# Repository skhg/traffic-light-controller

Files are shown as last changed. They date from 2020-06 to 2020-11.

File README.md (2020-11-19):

# traffic-light-controller

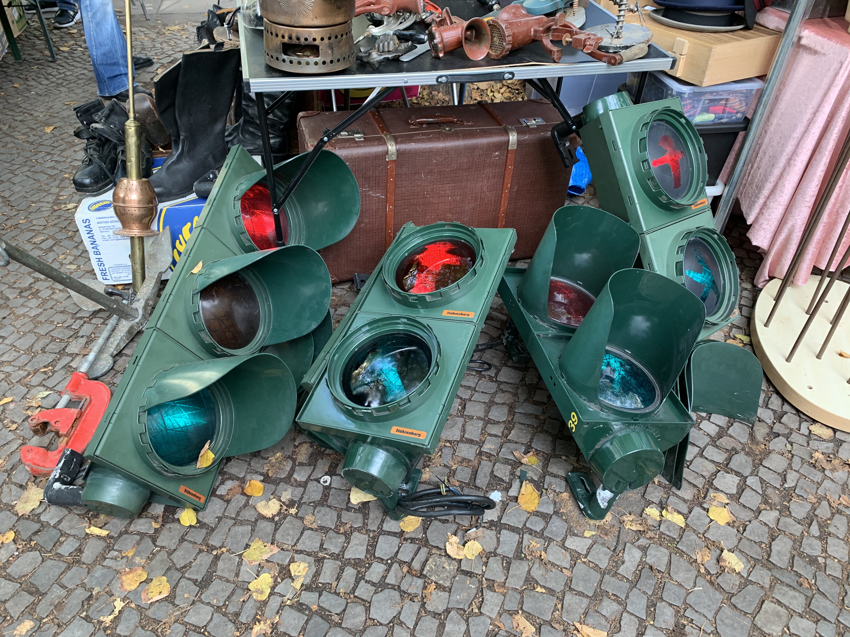
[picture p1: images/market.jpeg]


The [_Ampelmännchen_](https://en.wikipedia.org/wiki/Ampelm%C3%A4nnchen) are a popular symbol from East Germany, which display on the pedestrian traffic lights at every street corner. There's even a Berlin-based [retail chain](https://www.ampelmann.de/) that's inspired by their design.

I came across a set of secondhand Ampelmann signals at a flea market, and I wanted to control them from my phone. If you'd like to do the same, read on!

## Overview

**Health Warning:** This project uses 220V mains power. I am not an electrician. Follow these instructions at your own risk.

I wanted to build something with a _Berlin aesthetic_, and would be fun for visitors to my home to interact with. Unfortunately our visitor numbers [declined severely this year](https://en.wikipedia.org/wiki/COVID-19_pandemic), but still hoping for a great reaction in 2021...?

<p align="center"><br/>
 <i>Controlling the traffic lights from the webapp on iOS</i></p>

How does it work?
 1. The webapp runs in your browser
 1. It connects to a web server on the Arduino microcontroller
 1. The Arduino controls the lights using relays, which are [electronically-operated switches](https://en.wikipedia.org/wiki/Relay).
 1. When the lights change their state, the webapp will stay in sync
 1. ???
 1. Profit!

I used solid-state relays, which can be a bit more expensive than an [optocoupler relay](https://www.amazon.de/-/en/gp/product/B078Q326KT/ref=ppx_yo_dt_b_search_asin_title?ie=UTF8&psc=1) but don't make any [noise](https://youtu.be/FhQLq-eqfEc?t=2) as they switch, which is preferable for this project. To run the system we need a WiFi-capable, Arduino compatible microcontroller board - so the trusty [ESP8266 NodeMCU](https://en.wikipedia.org/wiki/NodeMCU) works perfectly here. 220V AC (mains) power is required anyway so there is no need for batteries or any low-power considerations.

The Arduino acts as a web application server (kind-of, see below), and also as an API server to control the lights themselves. Since we can have multiple users controlling the lights at once, each client subscribes to a WebSocket event stream, to get updates on the lights' status, without polling. More on this below too.

Since we have the option to run the lights in "party mode" where they pulse to a a rhythm, the Arduino code also needs to run some time-based logic that can't block anything else the board is doing. This isn't too difficult, and there are some useful [resources](https://forum.arduino.cc/index.php?topic=503368.0) online which explain how to "[do multiple things at once](https://forum.arduino.cc/index.php?topic=223286.0)" with arduino.

## Prerequisite knowledge
For anyone following this article i'm assuming a basic knowlegde of:
 * Electronics assembly techniques (soldering, wiring)
 * Microcontroller projects and concepts (Arduino)
 * Web technologies (HTTP, proxies and WebSockets)
 * Software lifecycle concepts (Deployment, versioning)
 * Software control flow concepts (Loops, functions, program state)

## Materials Required

For assembly:
 * 1 set of Ampelmann traffic lights
 * Assorted small [M2](https://www.amazon.de/-/en/gp/product/B07SGP8TWS/ref=ppx_yo_dt_b_search_asin_title?ie=UTF8&psc=1), [M3, M4](https://www.amazon.de/-/en/gp/product/B00B22VHPC/ref=ppx_yo_dt_b_asin_title_o00_s00?ie=UTF8&psc=1) nuts and bolts
 * A little [wooden board](https://www.amazon.de/-/en/gp/product/B07D76MKFY/ref=ppx_yo_dt_b_search_asin_title?ie=UTF8&psc=1) - for mounting our controller securely
 * Double-sided sticky tape - for mounting the temperature sensors
 
Electronic components:
 * 1 [NodeMCU v3 ESP8266](https://www.amazon.de/-/en/gp/product/B074Q2WM1Y/ref=ppx_yo_dt_b_search_asin_title?ie=UTF8&psc=1) - The microcontroller board
 * 1 Multiple Channel [Solid-State Relay](https://www.amazon.de/-/en/gp/product/B07DK6P9CV/ref=ppx_yo_dt_b_asin_title_o00_s00?ie=UTF8&psc=1) - the electronic switch which controls the lightbulbs
 * 2x [DHT11](https://www.amazon.de/-/en/gp/product/B07Q3H24LL/ref=ppx_yo_dt_b_search_asin_title?ie=UTF8&psc=1) - Temperature/humidity sensors
 * A [220V power cable](https://www.amazon.de/-/en/gp/product/B07NSSHP9S/ref=ppx_yo_dt_b_search_asin_title?ie=UTF8&psc=1) - Should capable of taking a few amps, you may also need to cut this apart for interior wiring
 * 2 10kΩ [resistors](https://www.amazon.de/-/en/gp/product/B07Q87JZ9G/ref=ppx_yo_dt_b_search_asin_title?ie=UTF8&psc=1) - Required to operate the DHT11 sensors
 * [Perfboard](https://www.amazon.de/-/en/gp/product/B07BDKG68Q/ref=ppx_yo_dt_b_search_asin_title?ie=UTF8&psc=1) - To solder everything together on
 * [Ribbon Cable](https://www.amazon.de/-/en/gp/product/B076CLY8NH/ref=ppx_yo_dt_b_search_asin_title?ie=UTF8&psc=1) - To connect to components off the main board, such as the temperature sensors and relay.
 * [JST Headers](https://www.amazon.de/YIXISI-Connector-JST-XH-Female-Adapter/dp/B082ZLYRRN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) - Plugs which will terminate the cable connections.
 * A generic USB power supply
 * A power strip
 
Other necessary basic tools:
 * Soldering iron
 * Pliers
 * Screwdriver
 * Wire stripper
 * Power drill

## Circuit diagram

Here's how the circuit looks in a block diagram showing all components laid out flat.

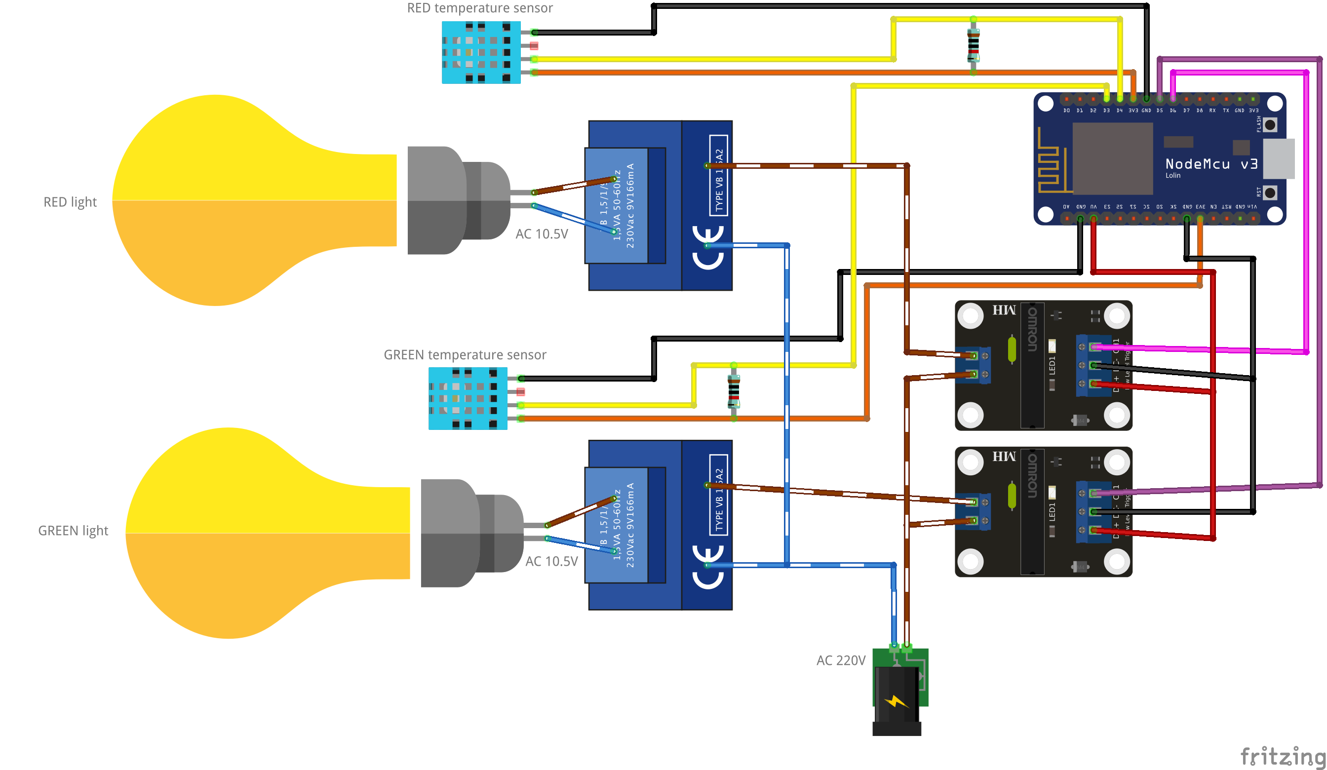
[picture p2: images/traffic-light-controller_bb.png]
Overview


And here's how the circuit board and temperature sensor board are wired on the perfboard. Depending on how you mount this inside the case, and what size perfboard is used, you may have more space to play around with.

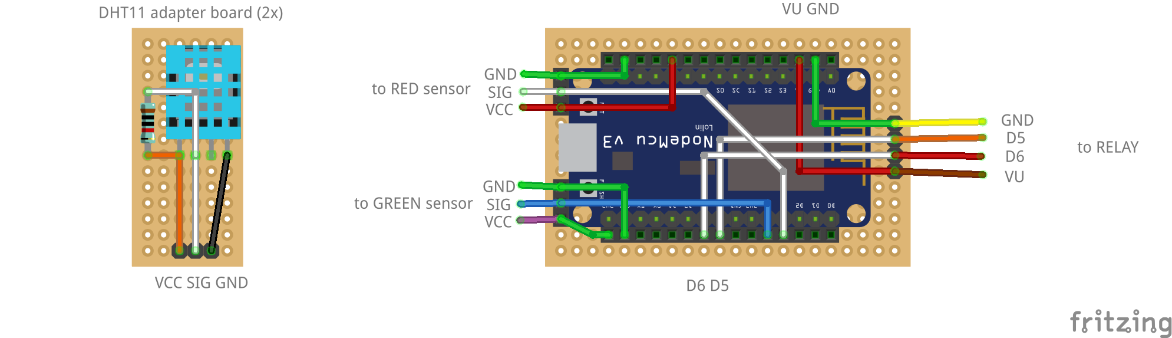
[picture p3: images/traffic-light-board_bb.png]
Board

<i>(Exported from Fritzing [file](traffic-light-board.fzz))</i>

## Construction

The traffic light comes with 2 steel mounts, which are hollow. At the front, it has two doors which open to reveal the bulbs, reflectors and the transformers behind. These traffic bulbs are designed to run on 10.5V (30VA) as is printed on the transformer label. Behind the reflector, there's actually a lot of empty space. In a normal traffic light installation, all the control logic would be handled by an external box, but we want to have everything self-contained. So we will make the most of the space available.

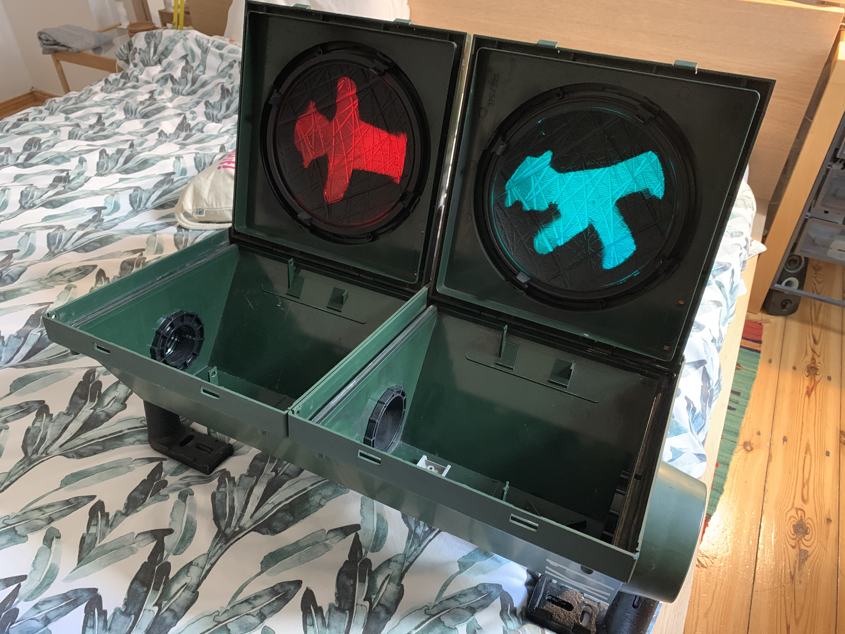
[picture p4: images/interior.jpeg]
Interior Empty Interior


The ESP8266 and the relay board are mounted onto a small wooden board, that itself is bolted to the back of the traffic light case.

The live and neutral wires coming from the 220V mains need to be split. Neutral connects to each of the transformers, as before. Live connects to two of the relays. Each of the relays then needs to be connected to neutral on both of the transformers. This completes the circuit, and when the relay is in it's "on" state, the light will come on.

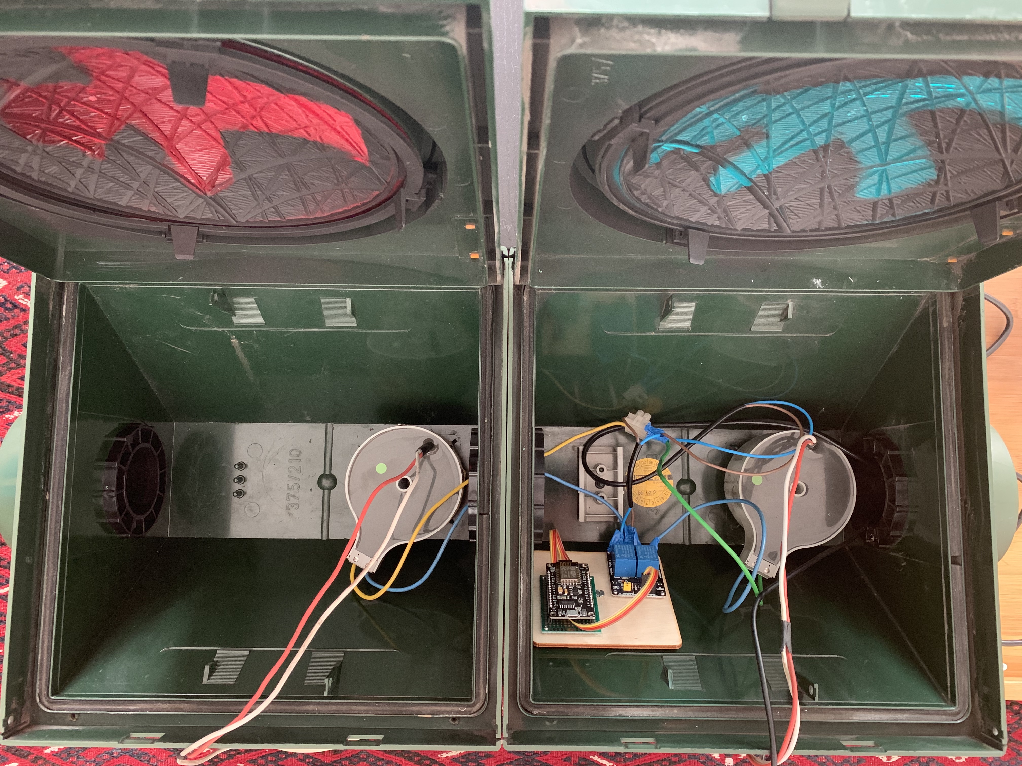
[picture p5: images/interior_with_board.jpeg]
Interior with board Interior with board v1


The two temperature sensors are mounted on to identical mini-perfboards. They are attached to the upper edge of each reflector section with double-sided sticky tape, and connected to the main board with ribbon cable.

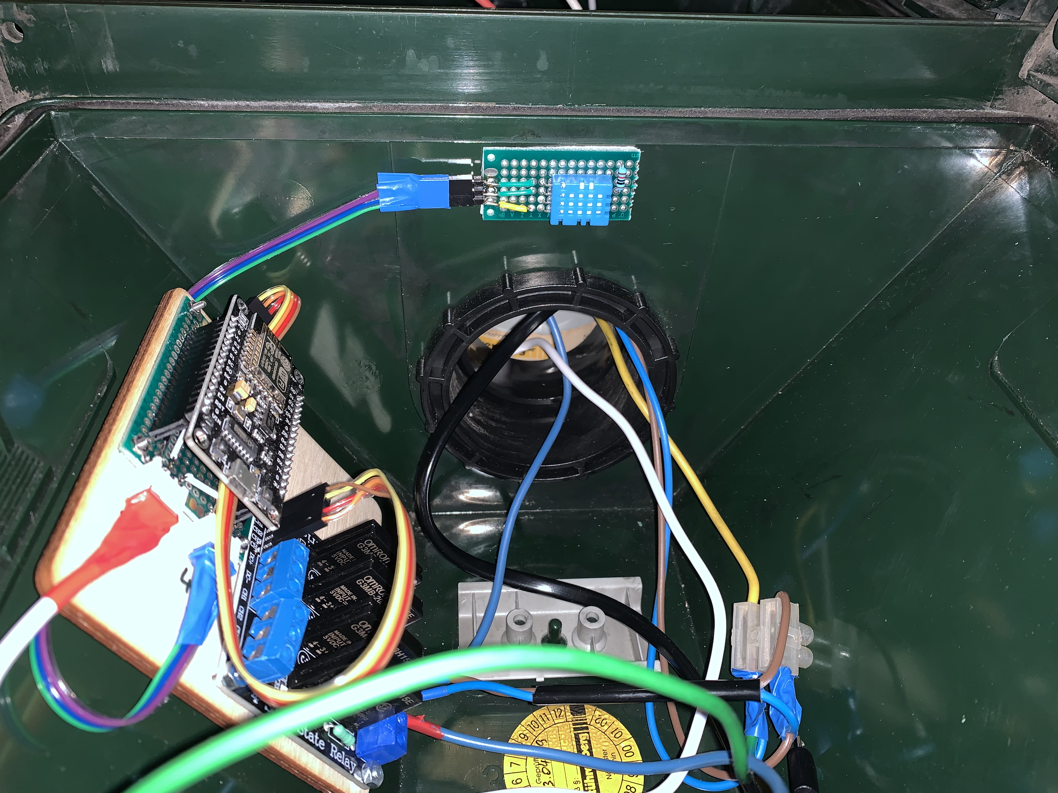
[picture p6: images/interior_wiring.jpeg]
Interior wiring


Once everything is hooked up, we can test it out, and close it up.

<p align="center"><br/>
<i>Testing the bulbs with the solid-state relay</i></p>

## Software

There are a few moving parts in the software here, so i've split this into a couple of sections.

### Overview

The software is intended to allow users on the same LAN to control the traffic light through a browser, without any prior authorisation needed. Security is not considered for this project. The browser shows the state of the system in real time.



Each device on your local network has it's own [private](https://en.wikipedia.org/wiki/Private_network) IP address (e.g. `192.168.1.20`). Some routers such as the FritzBox also let you browse by local hostnames, so that `192.168.1.20` is also accessible at `mydevice.fritz.box`. For the traffic light, the device hostname is `traffic-light` so we can visit it at `http://traffic-light.fritz.box`.

### Webapp architecture & performance

The webapp is a very simple responsive single-page application. It shows:
* Red on/off
* Green on/off
* Party mode on/off
* Temperature of the red and green enclosures
* Currently playing song information.

Code is under the [/webapp](/webapp) directory. No external dependencies are required since it's just relying on standard browser features, like [CSS transform](https://developer.mozilla.org/en-US/docs/Web/CSS/transform), [WebSockets](https://developer.mozilla.org/en-US/docs/Web/API/WebSocket), and [XHR](https://developer.mozilla.org/en-US/docs/Web/API/XMLHttpRequest/Using_XMLHttpRequest). You can preview the running application [here](http://jackhiggins.ie/traffic-light-controller/) although it won't control anything, since of course you're not on my LAN. If you visited it from the local network, at e.g. `http://traffic-light.fritz.box` it would work fully.

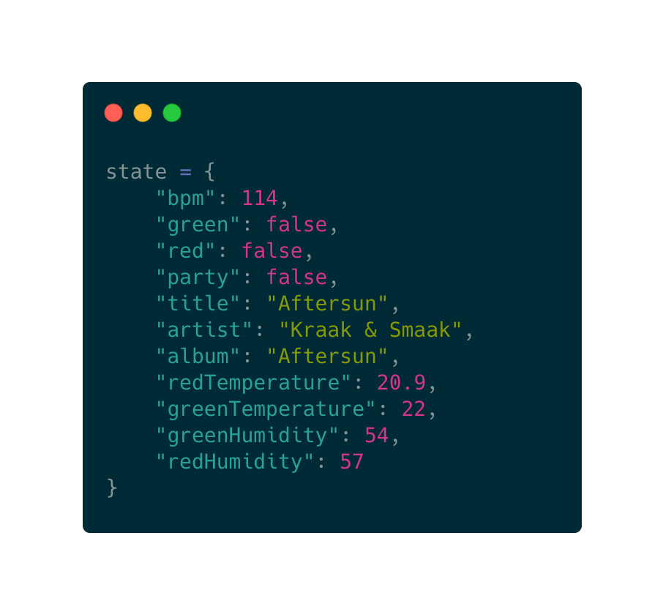
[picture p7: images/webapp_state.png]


Upon loading the page, the application makes a GET request to find the current status at `/api/status`, and then opens a WebSocket connection to the server on port `81`. Subsequent status updates will always come via the WebSocket, in order to keep multiple clients in sync. Each time a websocket event arrives, we apply the changes to a single global `state` object. Shortly afterwards, the `updateScreen()` method applies those changes to the DOM.

On startup we also detect if the user is on a mobile or desktop device, to handle either touch events or click events. We actually use the `touchend` event to send commands to the server, because this performed more reliably on the iPhone X. Swiping up from the bottom of the screen to exit Safari was firing the `touchstart` event, making it impossible to exit the app without turning on the green light!

Finally, we want to reduce load on the server wherever possible. Remember the ESP8266 is [running](https://docs.zerynth.com/latest/reference/boards/nodemcu3/docs/) on an _80MHz_ processor with only about _50kB_ of RAM. It is NOT a beefy device. So when the browser is inactive, we disconnect the websocket. When the tab or browser reopens, we again check for status, and reconnect the WebSocket.

### Webapp Deployment

The ESP8266 is busy handling API requests and timing code, so it doesn't have the necessary resources to serve the webapp itself. Also, making cosmetic changes to the webapp is difficult, if I need to physically connect to the hardware every time I want to apply an update.

The webapp's [index.html](/webapp/index.html) follows the single-page application principle that everything should be rendered by Javascript, making the HTML content itself very small. Like _550 bytes_ small. Everything else is loaded by the client's browser, without needing to make further calls to the server. So the webapp is actually hosted in its entirety [on GitHub Pages](http://jackhiggins.ie/traffic-light-controller/), a free [static site hosting tool](https://pages.github.com/). Hitting `/index.html` actually makes a proxy request to GitHub pages, and returns the result to the client browser.

Now we can change anything in the webapp, and the server is unaffected. Great! Well, almost...

### Webapp resource versioning

Most of the code for this webapp is in the CSS and JS files, not in `index.html` itself. Browsers cache any loaded files for an indeterminate period of time before it re-requests them. If index.html doesn't change, but we've deployed a new JS version, how will our clients know they need to load the new JS version?

When we push any new version of our code to the git `master` branch, a GitHub [Action](.github/workflows/deploy-gh-pages.yml) runs, that executes the deployment to GitHub Pages where the page is actually served to the public. The trick here is in appending the suffix `?version=latest` to the end of our own CSS and JS files, in the `index.html`. Before it copies the content to the `gh-pages` branch, the action uses the command `sed` to replace that "`latest`" with the value of the variable `$GITHUB_SHA`, which is actually the last commit ID on the `master` branch. (e.g. a value like `b43200422c4f5da6dd70676456737e5af46cb825`).

Then the next time a client visits the webapp, the browser will see a new, different value after the `?version=`, and request the new, updated JS or CSS file, which it will not have already cached.

### API

See the `setup(void)` method in `traffic-light-controller.ino` and the Arduino Code section for how this works in practice.

I decided to use both REST and WebSockets in tandem. REST is mostly used by clients to control the server. WebSockets are used to broadcast status information to clients. There are many tools like [Postman](https://www.postman.com/) which allow you to easily experiment with REST API's, so I found this more convenient.

**HTTP API:** Refer to the Swagger documentation [here](http://jackhiggins.ie/traffic-light-controller/docs/).

**WebSocket API:**
The websocket connection sends JSON blobs which the webapp uses to update its internal state. A websocket event can contain one or more fields to update. An example containing environmental info might look like:

```json
{
 "redTemperature" : 21.6,
 "greenTemperature" : 22.7,
 "greenHumidity" : 55,
 "redHumidity" : 59
}	
```

No data is current sent from the client to the server via the websocket, although this is possible.

### Arduino Code

The arduino code is all within a [single file](traffic-light-controller.ino) that includes explanatory comments.

It begins with a set of definitions for pin locations, library imports and hardcoded values for things like HTTP Content-Types and response code values. Following that are a set of variable which can change at runtime, all prefixed with underscores. A few objects are also initialised here, including those for the web server, web socket server, WiFi client, and temperature sensors. The "system clock" is maintained by the `_currentMillis` field.



After booting, the `setup(void)` method runs. After doing some pin setup, it creates the necessary mappings for the REST endpoints, and starts the servers listening for client requests. The `loop(void)` method is in charge of everything else. Each cycle it processes any pending web requests, updates the rhythm cycle, and reads the sensors if necessary. If we're in party mode, it will set the current flash/pulse state.

The rhythm (for party mode) is hardcoded to play the sequence in the field `RHYTHM_PATTERN`, but in theory it could be changed at runtime to anything else. Every time we call the `rhythm()` method, we use the current `_bpm` and `_currentMillis` values to work out what position we should be in the pattern. This is stored in the `_rhythmStep` field.

During the rhythm pattern, there are periods where both of the relays are actually switched off. But because the lights are incandescent bulbs, they don't start or stop emitting light instantly. It looks like the bulbs take about 1.7 seconds to switch fully on or off. So by adding a period within the pattern where both are switched off, we end up with a gentle pulsing pattern as the bulbs warm up and cool down.

In the `partyFlash()` method, we get the pattern item that is supposed to currently be displayed (or both are to be switched off) and call `lightSwitch(...)` with the appropriate parameters. `lightSwitch(...)` in turn calls `sendToWebSocketClients(...)` so that all connected clients are updated to the new state.

If the user simply clicks on one of the lights to turn it on or off, the process is similar, but handled as a REST request. One of the `handleX` methods is called, which validates the request, and in turn calls `lightSwitch(...)`.

At a more infrequent interval, we check the temperature of the two enclosures, and also send this via WebSocket to all clients. This is currently only used for informational purposes but it could be used to disable the lights when the temperature exceeds some safety limit.

## Thanks

Credit to [@mrcosta](https://github.com/mrcosta) for his help reviewing this article.

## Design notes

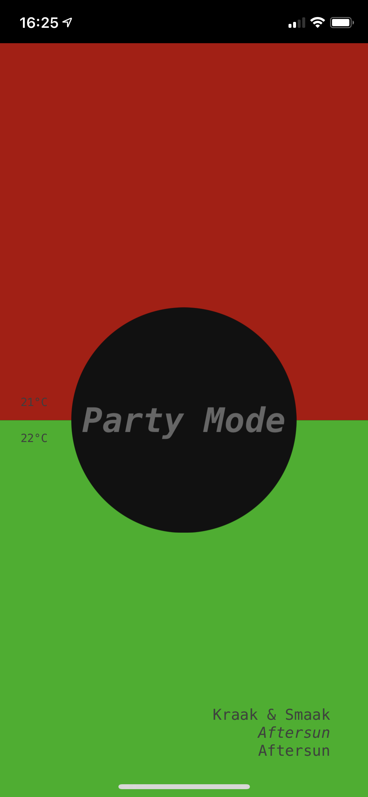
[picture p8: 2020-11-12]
images/webapp_screenshot.png

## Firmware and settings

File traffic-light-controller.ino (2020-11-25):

/**
 * Copyright 2020 Jack Higgins : https://github.com/skhg
 * All components of this project are licensed under the MIT License.
 * See the LICENSE file for details.
 */

#define RED_LIGHT D6
#define GREEN_LIGHT D5
#define SENSOR_RED_PIN D3
#define SENSOR_GREEN_PIN D4

#define RED_FLASH 0
#define GREEN_FLASH 1
#define BOTH_FLASH 2

#define DHT_SENSOR_TYPE DHT11

#include <Arduino.h>
#include <ESP8266WiFi.h>
#include <WiFiClient.h>
#include <ESP8266WebServer.h>
#include <ESP8266HTTPClient.h>
#include <home_wifi.h>
#include <ArduinoJson.h>
#include <ESPAsyncTCP.h>
#include <WebSocketsServer.h>
#include <DHT.h>

const String STATIC_CONTENT_INDEX_LOCATION =
"http://jackhiggins.ie/traffic-light-controller/";

const String HOST_NAME = "traffic-light";

const String EMPTY_STRING = "";

const String CONTENT_TYPE_TEXT_PLAIN = "text/plain";
const String CONTENT_TYPE_APPLICATION_JSON = "application/json";
const String CONTENT_TYPE_TEXT_HTML = "text/html";

const int HTTP_OK = 200;
const int HTTP_NO_CONTENT = 204;
const int HTTP_NOT_FOUND = 404;
const int HTTP_METHOD_NOT_ALLOWED = 405;
const int HTTP_BAD_REQUEST = 400;

const String METHOD_NOT_ALLOWED_MESSAGE = "Method Not Allowed";

const int TEMPERATURE_READ_INTERVAL_MILLIS = 10000;

WiFiClient WIFI_CLIENT;
HTTPClient HTTP_CLIENT;
ESP8266WebServer HTTP_SERVER(80);
WebSocketsServer WEB_SOCKET_SERVER(81);
DHT SENSOR_RED(SENSOR_RED_PIN, DHT_SENSOR_TYPE);
DHT SENSOR_GREEN(SENSOR_GREEN_PIN, DHT_SENSOR_TYPE);

boolean _redLit = false;
boolean _greenLit = false;
int _bpm = 100;
boolean _partyOn = false;
uint64_t _currentMillis = millis();
uint64_t _beatStartMillis = millis();
uint64_t _temperatureReadMillis = millis();
int _rhythmStep = 0;

String _currentTitle = "";
String _currentArtist = "";
String _currentAlbum = "";

double _redTemperature = 0.0;
double _redHumidity = 0.0;
double _greenTemperature = 0.0;
double _greenHumidity = 0.0;

const int RHYTHM_STEPS = 8;
const int RHYTHM_PATTERN[] = {
  RED_FLASH, GREEN_FLASH, RED_FLASH, GREEN_FLASH,
  RED_FLASH, GREEN_FLASH, BOTH_FLASH, BOTH_FLASH
};

void sendToWebSocketClients(String webSocketMessage) {
  WEB_SOCKET_SERVER.broadcastTXT(webSocketMessage);
}

void lightSwitch(int light, boolean newState) {
  digitalWrite(light, !newState);  // LOW means ON for the relay i'm using

  switch (light) {
    case RED_LIGHT: {
      if (newState != _redLit) {
        _redLit = newState;
        sendToWebSocketClients(redLightJson());
      }
      break;
    }
    case GREEN_LIGHT: {
      if (newState != _greenLit) {
        _greenLit = newState;
        sendToWebSocketClients(greenLightToJsonString());
      }

      break;
    }
  }
}

void partyFlash() {
  if (_rhythmStep % 2 == 1) {  // Any odd number
    lightSwitch(RED_LIGHT, false);
    lightSwitch(GREEN_LIGHT, false);
  } else {
    switch (RHYTHM_PATTERN[_rhythmStep / 2]) {
      case RED_FLASH: {
        lightSwitch(RED_LIGHT, true);
        lightSwitch(GREEN_LIGHT, false);
        break;
      }
      case GREEN_FLASH: {
        lightSwitch(RED_LIGHT, false);
        lightSwitch(GREEN_LIGHT, true);
        break;
      }
      case BOTH_FLASH: {
        lightSwitch(RED_LIGHT, true);
        lightSwitch(GREEN_LIGHT, true);
        break;
      }
    }
  }
}

void readSensors() {
  _currentMillis = millis();

  if (_currentMillis - _temperatureReadMillis >
        TEMPERATURE_READ_INTERVAL_MILLIS) {
    _temperatureReadMillis = _currentMillis;

    _redHumidity = SENSOR_RED.readHumidity();
    _redTemperature = SENSOR_RED.readTemperature();

    _greenHumidity = SENSOR_GREEN.readHumidity();
    _greenTemperature = SENSOR_GREEN.readTemperature();

    sendToWebSocketClients(sensorValuesToJsonString());
  }
}

String sensorValuesToJsonString() {
  String content;
  StaticJsonDocument<JSON_OBJECT_SIZE(4)> sensorsJson;
  sensorsJson["redTemperature"] = _redTemperature;
  sensorsJson["greenTemperature"] = _greenTemperature;
  sensorsJson["greenHumidity"] = _greenHumidity;
  sensorsJson["redHumidity"] = _redHumidity;
  serializeJson(sensorsJson, content);
  return content;
}

void rhythm() {
  int timingIntervalMillis = 60000 / (_bpm * 2);

  _currentMillis = millis();

  if (_currentMillis - _beatStartMillis > timingIntervalMillis) {
    _beatStartMillis = _currentMillis;

    if (_rhythmStep >= (RHYTHM_STEPS * 2) - 1) {
      _rhythmStep = 0;
    } else {
      _rhythmStep++;
    }
  }
}

void httpRootEventHandler() {
  if (HTTP_SERVER.method() != HTTP_GET) {
    HTTP_SERVER.send(HTTP_METHOD_NOT_ALLOWED, CONTENT_TYPE_TEXT_PLAIN,
      METHOD_NOT_ALLOWED_MESSAGE);
    return;
  }

  // Fetch content from source and forward it
  HTTP_CLIENT.begin(WIFI_CLIENT, STATIC_CONTENT_INDEX_LOCATION);
  HTTP_CLIENT.GET();

  HTTP_SERVER.sendHeader("Cache-Control", "no-cache");
  HTTP_SERVER.send(HTTP_OK, "text/html", HTTP_CLIENT.getString());
}

void httpNotFoundEventHandler() {
  String message = "File Not Found\n\n";
  message += "URI: ";
  message += HTTP_SERVER.uri();
  message += "\nMethod: ";
  message += (HTTP_SERVER.method() == HTTP_GET) ? "GET" : "POST";
  message += "\nArguments: ";
  message += HTTP_SERVER.args();
  message += "\n";
  for (uint8_t i = 0; i < HTTP_SERVER.args(); i++) {
    message += " " + HTTP_SERVER.argName(i) + ": " + HTTP_SERVER.arg(i) + "\n";
  }
  HTTP_SERVER.send(HTTP_NOT_FOUND, CONTENT_TYPE_TEXT_PLAIN, message);
}

void partyModeHttpEventHandler() {
  if (HTTP_SERVER.method() == HTTP_PUT) {
    _partyOn = true;
    HTTP_SERVER.send(HTTP_OK, CONTENT_TYPE_TEXT_PLAIN, "Party On!");
    Serial.println("Party started");
    sendToWebSocketClients(partyModeToJsonString());
  } else if (HTTP_SERVER.method() == HTTP_DELETE) {
    _partyOn = false;
    HTTP_SERVER.send(HTTP_OK, CONTENT_TYPE_TEXT_PLAIN, "Party's Over");
    Serial.println("Party ended");
    sendToWebSocketClients(partyModeToJsonString());
  } else if (HTTP_SERVER.method() == HTTP_GET) {
    HTTP_SERVER.send(HTTP_OK, CONTENT_TYPE_APPLICATION_JSON,
      partyModeToJsonString());
  } else {
    HTTP_SERVER.send(HTTP_METHOD_NOT_ALLOWED, CONTENT_TYPE_TEXT_PLAIN,
      METHOD_NOT_ALLOWED_MESSAGE);
  }
}

String partyModeToJsonString() {
  String content;
  StaticJsonDocument<JSON_OBJECT_SIZE(1)> partyJson;
  partyJson["party"] = _partyOn;
  serializeJson(partyJson, content);
  return content;
}

void redLightHttpEventHandler() {
  if (HTTP_SERVER.method() == HTTP_PUT) {
    lightSwitch(RED_LIGHT, true);
    HTTP_SERVER.send(HTTP_NO_CONTENT, CONTENT_TYPE_TEXT_PLAIN, EMPTY_STRING);
  } else if (HTTP_SERVER.method() == HTTP_DELETE) {
    lightSwitch(RED_LIGHT, false);
    HTTP_SERVER.send(HTTP_NO_CONTENT, CONTENT_TYPE_TEXT_PLAIN, EMPTY_STRING);
  } else if (HTTP_SERVER.method() == HTTP_GET) {
    HTTP_SERVER.send(HTTP_OK, CONTENT_TYPE_APPLICATION_JSON, redLightJson());
  } else {
    HTTP_SERVER.send(HTTP_METHOD_NOT_ALLOWED, CONTENT_TYPE_TEXT_PLAIN,
      METHOD_NOT_ALLOWED_MESSAGE);
  }
}

String redLightJson() {
  String content;
  StaticJsonDocument<JSON_OBJECT_SIZE(1)> redJson;
  redJson["red"] = _redLit;
  serializeJson(redJson, content);
  return content;
}

String greenLightToJsonString() {
  String content;
  StaticJsonDocument<JSON_OBJECT_SIZE(1)> greenJson;
  greenJson["green"] = _greenLit;
  serializeJson(greenJson, content);
  return content;
}

void greenLightHttpEventHandler() {
  if (HTTP_SERVER.method() == HTTP_PUT) {
    lightSwitch(GREEN_LIGHT, true);
    HTTP_SERVER.send(HTTP_NO_CONTENT, CONTENT_TYPE_TEXT_PLAIN, EMPTY_STRING);
  } else if (HTTP_SERVER.method() == HTTP_DELETE) {
    lightSwitch(GREEN_LIGHT, false);
    HTTP_SERVER.send(HTTP_NO_CONTENT, CONTENT_TYPE_TEXT_PLAIN, EMPTY_STRING);
  } else if (HTTP_SERVER.method() == HTTP_GET) {
    HTTP_SERVER.send(HTTP_OK, CONTENT_TYPE_APPLICATION_JSON,
      greenLightToJsonString());
  } else {
    HTTP_SERVER.send(HTTP_METHOD_NOT_ALLOWED, CONTENT_TYPE_TEXT_PLAIN,
      METHOD_NOT_ALLOWED_MESSAGE);
  }
}

void statusHttpEventHandler() {
  if (HTTP_SERVER.method() != HTTP_GET) {
    HTTP_SERVER.send(HTTP_METHOD_NOT_ALLOWED, CONTENT_TYPE_TEXT_PLAIN,
      METHOD_NOT_ALLOWED_MESSAGE);
  } else {
    String content;

    StaticJsonDocument<JSON_OBJECT_SIZE(8) + 1000> statusJson;
    statusJson["bpm"] = _bpm;
    statusJson["green"] = _greenLit;
    statusJson["red"] = _redLit;
    statusJson["party"] = _partyOn;
    statusJson["title"] = _currentTitle;
    statusJson["artist"] = _currentArtist;
    statusJson["album"] = _currentAlbum;
    statusJson["redTemperature"] = _redTemperature;
    statusJson["greenTemperature"] = _greenTemperature;
    statusJson["greenHumidity"] = _greenHumidity;
    statusJson["redHumidity"] = _redHumidity;
    serializeJson(statusJson, content);

    HTTP_SERVER.send(HTTP_OK, CONTENT_TYPE_APPLICATION_JSON, content);
  }
}

void tempoHttpEventHandler() {
  if (HTTP_SERVER.method() == HTTP_PUT) {
    if (HTTP_SERVER.hasArg("plain") == false) {
      HTTP_SERVER.send(HTTP_BAD_REQUEST, CONTENT_TYPE_TEXT_PLAIN,
        "Missing body");
    } else {
      StaticJsonDocument<JSON_OBJECT_SIZE(1) + 10> bpmJson;
      deserializeJson(bpmJson, HTTP_SERVER.arg("plain"));
      _bpm = bpmJson["bpm"];
      Serial.println("BPM is now: " + String(_bpm));
      HTTP_SERVER.send(HTTP_NO_CONTENT, CONTENT_TYPE_TEXT_PLAIN, EMPTY_STRING);
      sendToWebSocketClients(tempoToJsonString());
    }
  } else if (HTTP_SERVER.method() == HTTP_GET) {
    HTTP_SERVER.send(HTTP_OK, CONTENT_TYPE_APPLICATION_JSON,
      tempoToJsonString());
  } else {
    HTTP_SERVER.send(HTTP_METHOD_NOT_ALLOWED, CONTENT_TYPE_TEXT_PLAIN,
      METHOD_NOT_ALLOWED_MESSAGE);
  }
}

String tempoToJsonString() {
  String content;
  StaticJsonDocument<JSON_OBJECT_SIZE(1)> tempoJson;
  tempoJson["bpm"] = _bpm;
  serializeJson(tempoJson, content);
  return content;
}

void songHttpEventHandler() {
  if (HTTP_SERVER.method() == HTTP_PUT) {
    if (HTTP_SERVER.hasArg("plain") == false) {
      HTTP_SERVER.send(HTTP_BAD_REQUEST, CONTENT_TYPE_TEXT_PLAIN,
        "Missing body");
    } else {
      StaticJsonDocument<JSON_OBJECT_SIZE(3) + 1000> newSongJson;
      deserializeJson(newSongJson, HTTP_SERVER.arg("plain"));
      const char* artist = newSongJson["artist"];
      _currentArtist = artist;
      const char* album = newSongJson["album"];
      _currentAlbum = album;
      const char* title = newSongJson["title"];
      _currentTitle = title;
      Serial.println("Song is now: " + _currentTitle + " from "+ _currentAlbum +
        " by " + _currentArtist);
      HTTP_SERVER.send(HTTP_NO_CONTENT, CONTENT_TYPE_TEXT_PLAIN, EMPTY_STRING);
      sendToWebSocketClients(songToJsonString());
    }
  } else if (HTTP_SERVER.method() == HTTP_GET) {
    HTTP_SERVER.send(HTTP_OK, CONTENT_TYPE_APPLICATION_JSON,
      songToJsonString());
  } else if (HTTP_SERVER.method() == HTTP_DELETE) {
    _currentArtist = "";
    _currentAlbum = "";
    _currentTitle = "";
    Serial.println("Song ended");
    HTTP_SERVER.send(HTTP_NO_CONTENT, CONTENT_TYPE_TEXT_PLAIN, EMPTY_STRING);
    sendToWebSocketClients(songToJsonString());
  } else {
    HTTP_SERVER.send(HTTP_METHOD_NOT_ALLOWED, CONTENT_TYPE_TEXT_PLAIN,
      METHOD_NOT_ALLOWED_MESSAGE);
  }
}

String songToJsonString() {
  String content;
  StaticJsonDocument<JSON_OBJECT_SIZE(3) + 1000> changedSongJson;
  changedSongJson["title"] = _currentTitle;
  changedSongJson["artist"] = _currentArtist;
  changedSongJson["album"] = _currentAlbum;
  serializeJson(changedSongJson, content);
  return content;
}

void webSocketEventHandler(uint8_t num, WStype_t type, uint8_t * payload,
  size_t length) {
  IPAddress ip = WEB_SOCKET_SERVER.remoteIP(num);

  switch (type) {
    case WStype_DISCONNECTED: {
      Serial.println("WebSocket client disconnected.");
      break;
    }
    case WStype_CONNECTED: {
      Serial.print("WebSocket client at ");
      Serial.print(ip);
      Serial.println(" connected.");
      break;
    }
  }
}

void setup(void) {
  Serial.begin(115200);

  SENSOR_RED.begin();
  SENSOR_GREEN.begin();

  pinMode(RED_LIGHT, OUTPUT);
  pinMode(GREEN_LIGHT, OUTPUT);

  digitalWrite(RED_LIGHT, HIGH);
  digitalWrite(GREEN_LIGHT, HIGH);

  WiFi.begin(WIFI_SSID, WIFI_PASSWORD);
  WiFi.hostname(HOST_NAME);

  Serial.println(EMPTY_STRING);

  // Wait for connection
  while (WiFi.status() != WL_CONNECTED) {
    delay(500);
    Serial.print(".");
  }
  Serial.println(EMPTY_STRING);
  Serial.print("Connected to ");
  Serial.println(WIFI_SSID);
  Serial.print("Access at http://");
  Serial.print(WiFi.localIP());
  Serial.print("/ or http://");
  Serial.print(HOST_NAME);
  Serial.println("/");

  HTTP_SERVER.on("/", httpRootEventHandler);

  HTTP_SERVER.on("/api/red", redLightHttpEventHandler);
  HTTP_SERVER.on("/api/green", greenLightHttpEventHandler);
  HTTP_SERVER.on("/api/tempo", tempoHttpEventHandler);
  HTTP_SERVER.on("/api/party", partyModeHttpEventHandler);
  HTTP_SERVER.on("/api/status", statusHttpEventHandler);
  HTTP_SERVER.on("/api/song", songHttpEventHandler);

  HTTP_SERVER.onNotFound(httpNotFoundEventHandler);

  HTTP_SERVER.begin();
  Serial.println("HTTP server started");

  WEB_SOCKET_SERVER.begin();

  // Disconnect after a single failed heartbeat
  WEB_SOCKET_SERVER.enableHeartbeat(1000, 1000, 1);
  WEB_SOCKET_SERVER.onEvent(webSocketEventHandler);
}

void loop(void) {
  HTTP_SERVER.handleClient();
  rhythm();
  readSensors();

  if (_partyOn) {
    partyFlash();
  }
}

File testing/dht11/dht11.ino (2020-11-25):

/**
 * Copyright 2020 Jack Higgins : https://github.com/skhg
 * All components of this project are licensed under the MIT License.
 * See the LICENSE file for details.
 */

#include <DHT.h>

#define TEMPSENSOR_RED_PIN D3
#define TEMPSENSOR_GREEN_PIN D4
#define DHT_SENSOR_TYPE DHT11

DHT TEMP_SENSOR_RED(TEMPSENSOR_RED_PIN, DHT_SENSOR_TYPE);
DHT TEMP_SENSOR_GREEN(TEMPSENSOR_GREEN_PIN, DHT_SENSOR_TYPE);

void setup() {
  Serial.begin(115200);

  TEMP_SENSOR_RED.begin();
  TEMP_SENSOR_GREEN.begin();
}

void loop() {
  delay(5000);

  Serial.println("Red Sensor");
  double hum = TEMP_SENSOR_RED.readHumidity();
  double temp = TEMP_SENSOR_RED.readTemperature();
  Serial.print("Humidity: ");
  Serial.print(hum);
  Serial.print(" %, Temp: ");
  Serial.print(temp);
  Serial.println(" Celsius");

  Serial.println("---");

  Serial.println("Green Sensor");
  hum = TEMP_SENSOR_GREEN.readHumidity();
  temp = TEMP_SENSOR_GREEN.readTemperature();
  Serial.print("Humidity: ");
  Serial.print(hum);
  Serial.print(" %, Temp: ");
  Serial.print(temp);
  Serial.println(" Celsius");
}

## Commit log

2020-06-04 add some stuff for the apple home connection
    [traffic-light-controller.fzz]
2020-06-08 add non-functional party mode button, endpoint for tempo, and remove homepod stuff
2020-06-12 make the HTML code a global variable, reduce unnecessary logging and swap the red/green pins after putting in the new relay
    [traffic-light-controller.ino]
2020-06-12 switch to /api for api calls
2020-06-16 Clarify the split between application code and static content serving code (#2)
    * cleanup repeated strings
    * cleanup the .ino file and move static content to external .h files generated using a .py script
    * newlines
    * shorter code
    [traffic-light-controller.ino]
2020-06-17 Second web socket attempt (#4)
    * rename setup method
    * wip, realised i should not be using json serialisers globally
    * make the page html5
    * use the json doc correctly (non global)
    * capitalise var names for websocket and http servers
    * remove ezTime stuff again
    * send state for most things using websocket
    * use async TCP
    * correctly notify clients when BPM or party status changes
    * disconnect websocket when window is unloaded or in the background
    * don't use opacity which is not supported by marina's phone
    [traffic-light-controller.ino]
2020-06-19 Temperature sensors (#7)
    * testing dht11 and diagram
    * comments
    * diagram and testing
    * read temperature from sensors every 10 seconds
    * change the background colour to black
    * add divs for displaying the temperature data
    [traffic-light-board.fzz, traffic-light-controller.fzz]
2020-11-12 Nicer documentation (#9)
    * add more accurate diagrams for docs
    * Update README.md
    * Update README.md
    * Update README.md
    * Update README.md
    * Update README.md
    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
    [traffic-light-board.fzz, traffic-light-controller.fzz]
2020-11-12 move images to /images dir
    [traffic-light-board.fzz, traffic-light-controller.fzz]
2020-11-25 Documentation and linting (#12)
    * styleLint
    * test validation of swagger docs
    * fix
    * add jsdoc rule to eslint
    * refactor js app and add jsdocs
    * add some comments
    * try installing cpplint
    * run cpp linter
    * uses python setup
    * linter fixes
    * linting fixes
    * rename cpp methods for clarity
    [traffic-light-controller.ino]
2020-11-25 Arduino test compile (#13)
    * try to build arduino project
    * custom home wifi library
    * include required libraries
    * remove spaces
    * try just with 2 libs
    * just 1 library
    * just DHT library
    * add 2 more required libs
    * custom async TCP
    * delibrately break code
    * Revert "delibrately break code"
    This reverts commit 3fc69c784d3ee20cd185e3a32c89d997d286646d.
